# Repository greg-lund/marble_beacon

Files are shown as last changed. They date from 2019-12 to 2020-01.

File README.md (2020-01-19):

# Marble Urban Beacon Deployment System

This repository acts as an assembly guide for the COM Deployment System, and all the info that you need to build them can be found here.
For completion of this project, 20 beacons will be manufactured as well as 6-8 modified deployment systems. 
Instructions and files for the beacon are located in the beacon directory. The same is true for the deployment system. 

### BOM
The individual instruction pages include required parts, but an extensive bill of materials can be found here: <a href="https://docs.google.com/spreadsheets/d/1t7GFp-e4R7KjWGMSAGMCT9jzbI4BLS0B_l41IRGNlJQ/edit?usp=sharing" target="blank">BOM</a>.

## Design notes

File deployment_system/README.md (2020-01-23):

# Deplyoment System Assembly Instructions

All the information and part files that you need to build a deployment mechanism can be found here. I would recommend starting the 3D prints first, as the 3D prints are the most time consuming. Gathering all of the components beforehand, as well as lasercutting everything out first will make assembly much easier. 

### Parts List
Part | Quantity
-------- | --------
2020 Aluminum Extrusion | 2 x 15.75"<br>1 x 14.25"<br>3 x 10"<br>9 x 6"<br>6 x 3"
V-Slot Aluminum Extrusion | 3 x 11.75"
90&deg; 2020 bracket | 24
45&deg; 2020 bracket | 6
Nema 17 Stepper Motor | 3
Stepper Motor Bracket | 3
GT2 Pulley - 16 Tooth | 3
GT2 Idler Kit | 1
GT2 Belt x 102.5mm | 3
V-Wheel Kit | 18
M5 x 40mm Bolt | 18
M5 x 16mm Bolt | 9
M4 x 10mm Bolt | 12
M3 x 8mm Bolt | 12
M3 x 10mm Bolt | 12
M5 Spacer x 20mm | 18
M3 Spacer x 8mm | 2
M3 Spacer x 4mm | 4
CNC Shield with Arduino | 1
DRV8825 Driver Board | 3
Limit Switch Board | 3

In addition to all of the purchased components, there are various 3D printed and lasercut acrylic pieces that need to finished before the full assembly can begin. All of the files, for both 3D print and lasercut, can be found in the STL and DXF folders.

### 3D Printed Parts
Part File Name | Quantity | Notes
-------- | -------- | --------
belt\_bracket.STL | 3 | Onyx is prefered as these will be tapped<br>and support the whole weight of the beacon.
belt\_bracket\_top.STL | 3 | Onyx is prefered as these will be tapped<br>and support the whole weight of the beacon.

Assuming that assembly of the beacons have begun, you should not have to lasercut the gantry gripper piece nor the limit switch mounts. For these parts use 1/4" acrylic. All the other parts needed have been organized into a larger file to be cut out of a 12"x24" sheet. Each sheet will produce 5 of the 3 required gantry plates, and 2 of the 1 required stepper motor plate. This means that eventually 3 more of the gantry plates will need to be cut out. The individual files are also included in the directory DXF\_FULL.

### Lasercut Acrylic Pieces
Part File Name | Quantity | Notes
-------- | -------- | --------
deployment\_sheet.DXF | 1 | Use a full 1/4"x12"x24" sheet of acrylic

## Step 1: Assemble the 8020 Frame

#### Parts Needed:
- 2 x 15.75" 2020
- 1 x 14.25" 2020
- 3 x 10" 2020
- 3 x 11.75" V-Slot
- 6 x 90&deg; 2020 Bracket
- 6 x 45&deg; 2020 Bracket
- 12 x 2020 T-Slot Nut
- 12 x M5 x 8mm Bolt

Begin by tapping the ends of the 10" 2020 extrusions with an M5 tap. Assemble the frame as is shown in the drawing, below.

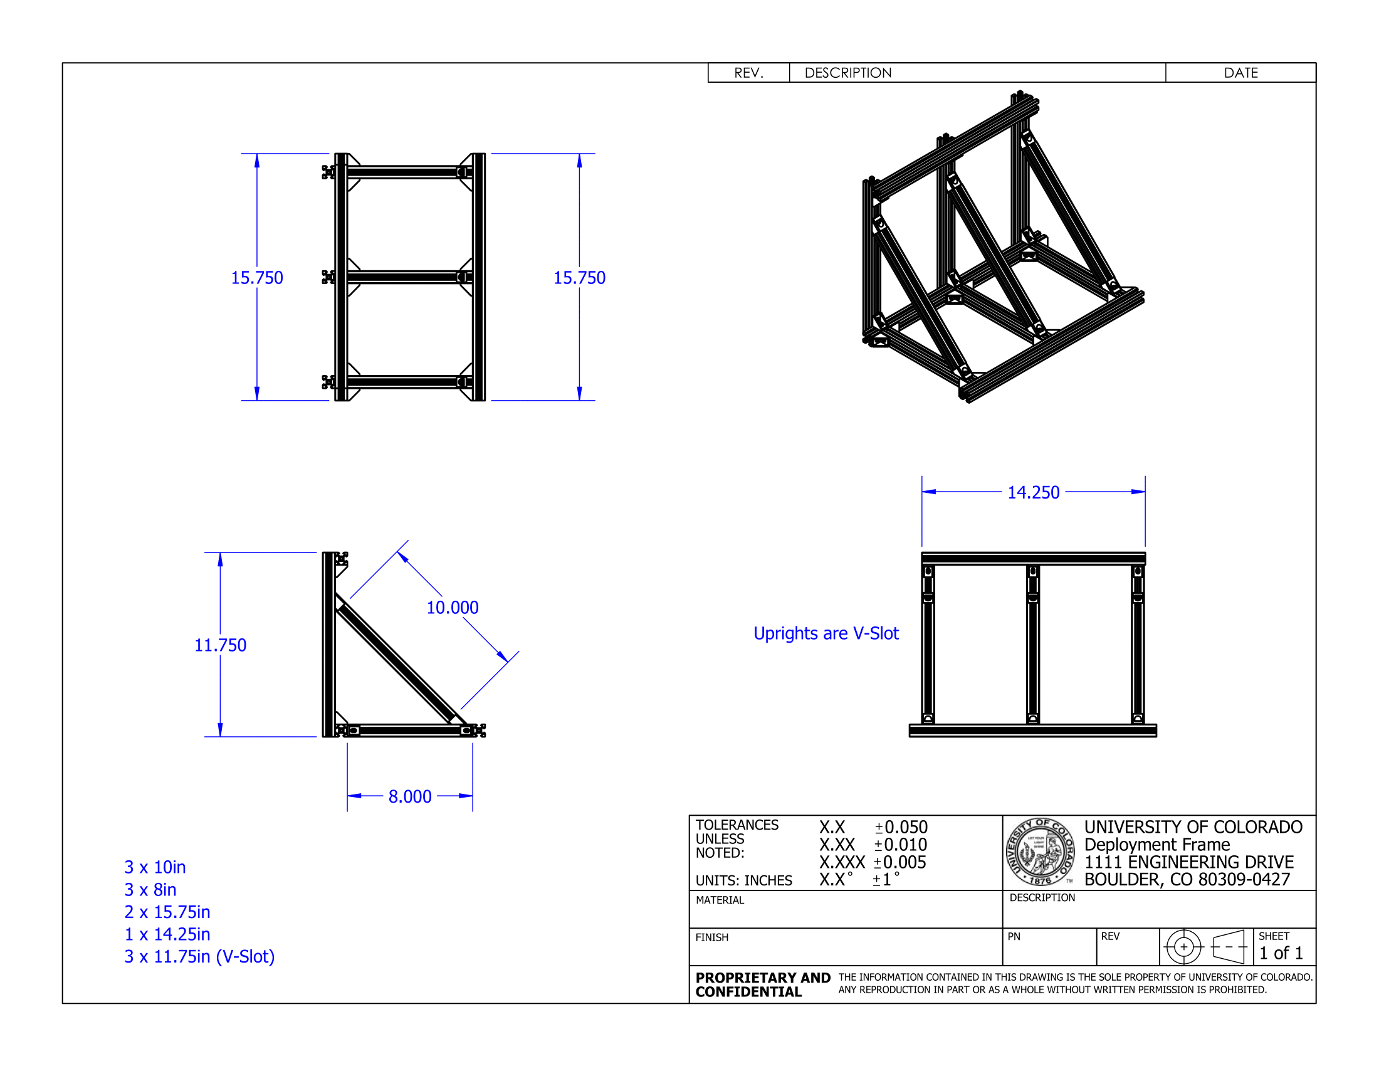
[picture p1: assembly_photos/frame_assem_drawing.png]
frame_assembly


## Step 2: Stepper Motor Mounting

#### Parts Needed:
- Stepper plate acrylic panel
- 3 x Nema 17 stepper motors
- 3 x Stepper motor bracket
- 3 x 16 tooth GT2 pulley
- 3 x T-nut and bolt
- 12 x M4 x 10mm Bolt and Nut
- 12 x M3 x 8mm Bolt and Nut
- 2020 frame assembly

Begin by attatching the motor brackets, as well as motors to the acrylic plate. Use the M4 and M3 screws here. Attach the motor assembly to the top of the frame assembly via the t-nuts and M5 holes in the plate. Attatch the pulleys at any point.

## Step 3: Fork Subassemblies

#### Parts Needed:
- 9 x 6" 2020 
- 6 x 3" 2020
- 18 x 90&deg; 2020 bracket
- 33 x T-nut and bolt
- 3 x Side plate acrylic panel
- 3 x Gantry gripper acrylic panel
- 18 x M5 x 40mm bolt
- 18 x 20mm M5 spacer
- 18 x V-Wheel kit

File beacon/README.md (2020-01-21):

# COM Beacon Assembly Instructions

All the information and part files that you need to build a COM beacon can be found here. I would recommend starting the 3D prints first, especially the electronics core rail pieces, as the 3D prints are the most time consuming. Gathering all of the components beforehand, as well as lasercutting everything out first will make assembly much easier. 

### Parts List
Part | Quantity 
-------- | --------
Power Antenna | 1
Rock64 with eMMC | 1
Battery Pack | 1
Doodle Radio | 1
12V to 5V Automotive Regulator | 1
FeatherLight Latching Relay | 1
Pushbutton with Light | 1
DPDT Switch | 2
DC Jack | 1
XT60 Connector (Male + Female) | 1
12 pin molex connector with wires (5040511201) | 1
4 Pin Molex (Male + Female) | 1
206485 9 Pin Circular Connector (Male + Female) | 1
RJ45 Connector | 1
3.5mm DC Jack - 90&deg; | 1
M2.5 Nylon Standoff and Nut | 8
M2.5 x 5mm bolt | 8
1/4" Wire Loom | 2 ft
Assorted Zipties | 

In addition to all of these purchased components, there are a variety of 3D printed and lasercut acrylic parts that need to be made before beginning the full assembly. The appropriate files for the 3D printer and lasercutter can be found in the STL and DXF directories, respectively. 

### 3D Printed Parts
Part's File Name | Quantity | Notes
-------- | -------- | --------
beacon\_foot.STL | 8 | PLA should be fine
electronics\_core\_rail.STL | 12 | PLA should be fine
lid\_bracket.STL | 1 | Use high infill or Onyx<br>as these require holes to be tapped
package\_bracket.STL | 6 | Use high infill or Onyx<br>as these require holes to be tapped

The lasercut parts for a single beacon have been organized into larger files to be cut out of 1/8"x12"x24" acrylic sheets. There are two main files that take up most of their sheets, and the electronics core must be cut separately.

### Lasercut Parts
Part's File Name | Quantity | Notes
-------- | -------- | --------
beacon\_sheet.dxf | 1 | Use a full 18"x24" sheet

The beacon\_sheet.dxf file has all of the lasercut components to create a single beacon. Take care in aligning the cut as the pieces are a tight fit on the sheet. If an individual part's DXF is required it can be found in the FULL\_DXF directory.

## Step 1: Wiring the Front Panel

#### Parts Needed:
- Pushbutton
- DC jack
- 2 x DPDT switch
- 206485 circular connector, wire mount 
- Front acrylic panel
- Assorted wire

Begin by soldering long wires onto all of the used terminals of the pushbutton, dc jack and switches. Use thicker guage for the GND, +12V and battery connections on the pushbutton and DC jack.

Mount all the components onto the front panel as shown in the photo below. Make connections and crimp connectors for the 206485 socket contacts according to the pinouts below.

#### 206485 Connector Pinout
Pin | Connection
-------- | --------
1 | +12V
2 | Battery Positive
3 | +3.3V
4 | SET
5 | GND
6 | UNSET
7 | Pi2: 3
8 | Pi2: 5
9 | NC

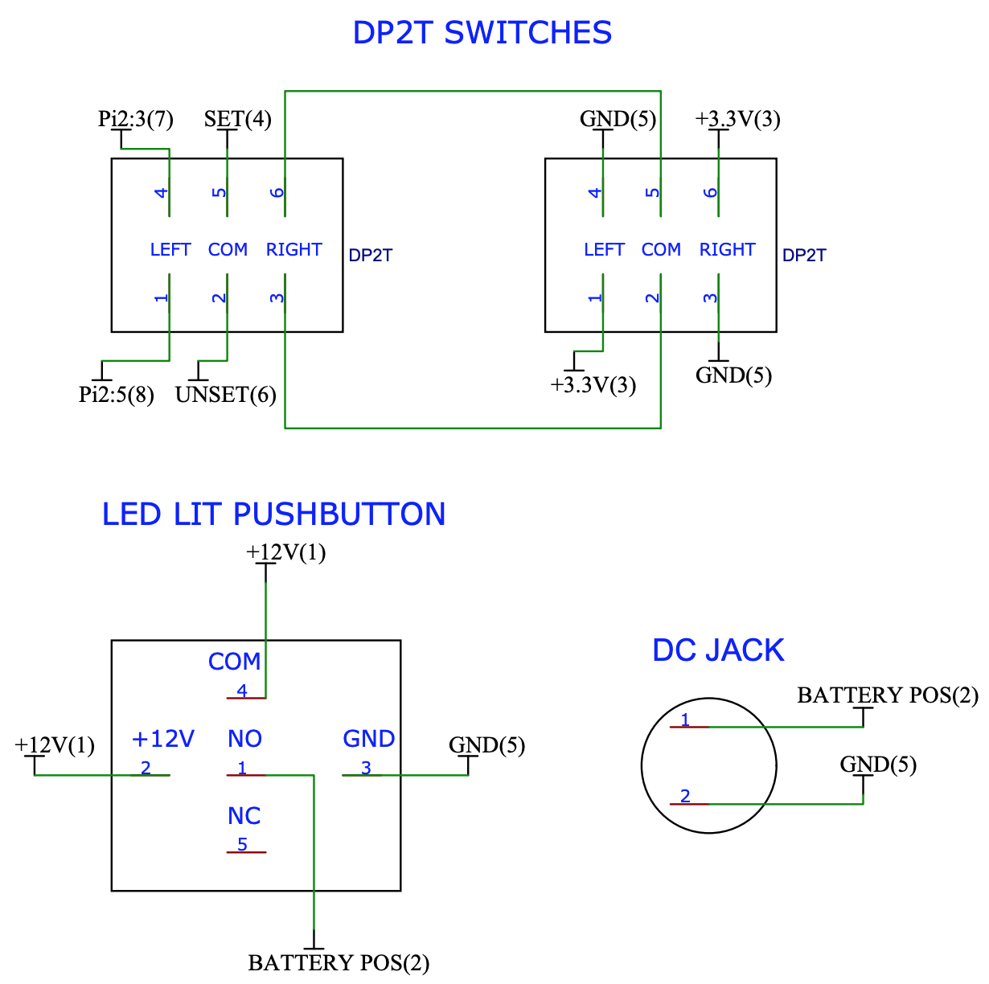
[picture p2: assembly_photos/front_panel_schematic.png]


## Step 2: Assembling the Acrylic Box

#### Parts Needed:
- The four acrylic side panels(including the wired front panel)
- Bottom acrylic panel
- 12 electronics core rail 3D prints

Begin by gluing the electronics core rail to the two identical, larger side panels. If you can't find a side plate raile template piece, lasercut one out. Line up the template with a side plate, and attach it via the two M3 screw holes. Either use superglue or acrylic cement to glue the 6 rail pieces to the plate. Don't forget to use clamps and ensure the flanges are facing eachother. Do the same on the other side, ensuring they are opposite and will fit up together.

Once the glue on the side panels has cured, glue all the pieces together, ensuring that the mounting holes for the switches and charging ports are on top and that the holes in the base plate are opposite those ports. Use either superglue or acrylic cement. Tape or clamp everything together ensuring that everything is square.

## Step 3: Assembling the Electronics Core

#### Parts Needed:
- Electronics core acrylic panel
- Battery
- XT60 pin and socket
- Rock64
- Latching relay
- Step-down converter
- Doodle radio
- 206485 panel mount connector 
- 12 pin molex connector with wires (5040511201)
- RJ45 connector
- M2.5 standoffs and screws
 
Begin by screwing all of the standoffs on to the electronics core panel. Zip tie the battery and radio, then screw down the rest of the components as shown. Solder a XT60 connector to the battery.

Wire all of the components together and crimp connections for the 206485 connector as well as the RJ45 connector. Follow the schematic below and the pinout for the 206485 connector above. Pinout diagrams for the doodle radio and RJ45 connector can be found in the wiring folder.

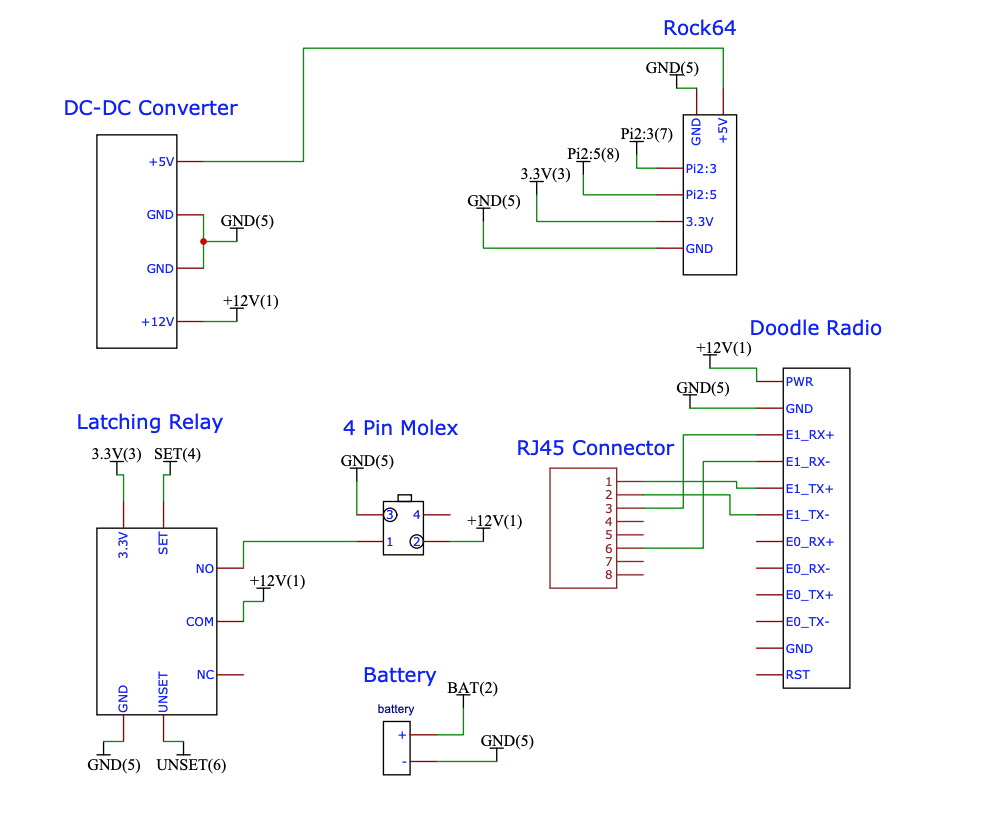
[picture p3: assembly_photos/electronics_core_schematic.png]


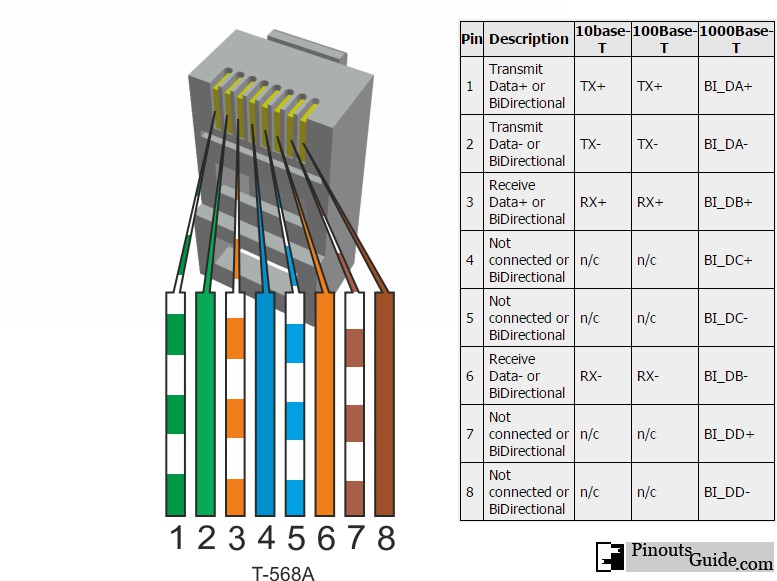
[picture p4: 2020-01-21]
beacon/wiring/rj45_pinout.jpg

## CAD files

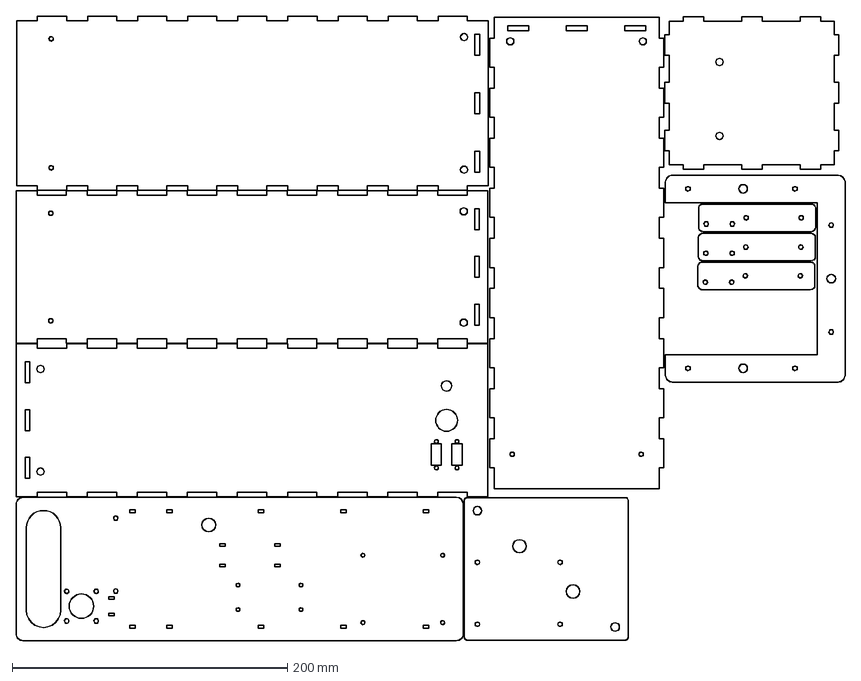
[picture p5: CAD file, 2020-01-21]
beacon/DXF/beacon_sheet.dxf
602.3 x 453.5 mm

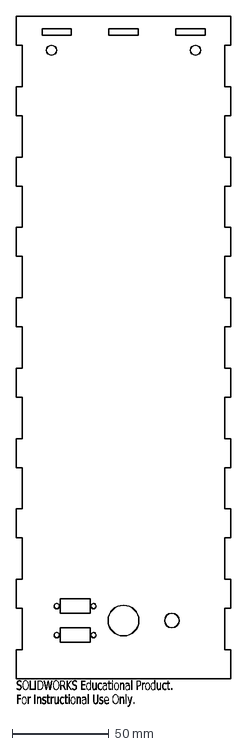
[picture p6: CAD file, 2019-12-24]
beacon/DXF/DXF_FULL/side_plate_C.DXF
SOLIDWORKS Educational Product.
For Instructional Use Only.

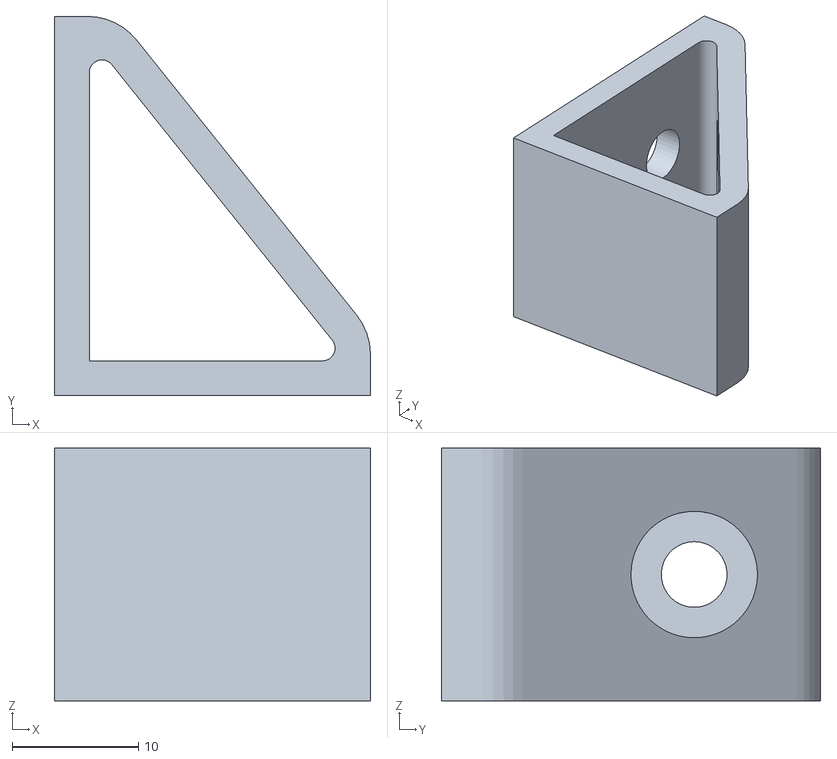
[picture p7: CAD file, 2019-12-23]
beacon/STL/beacon_foot.STL
25.0 x 30.0 x 20.0

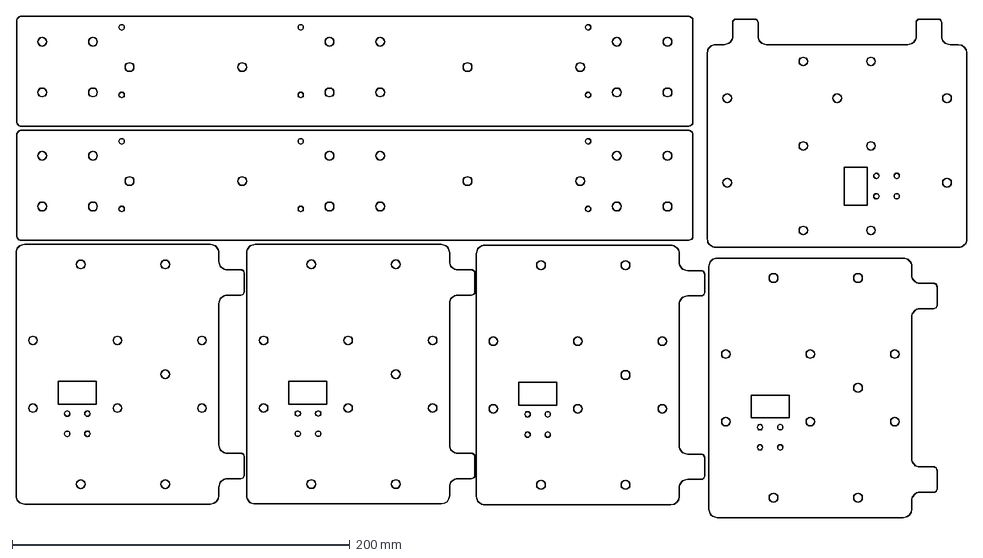
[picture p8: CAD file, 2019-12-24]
deployment_system/DXF/deployment_sheet.dxf
562.6 x 296.6 mm

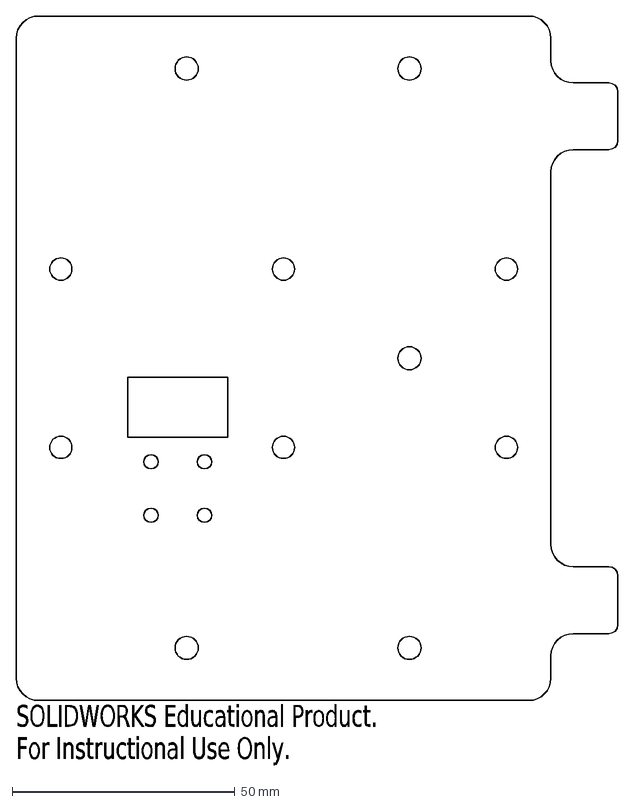
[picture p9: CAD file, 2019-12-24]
deployment_system/DXF/DXF_FULL/side_plate.DXF
SOLIDWORKS Educational Product.
For Instructional Use Only.

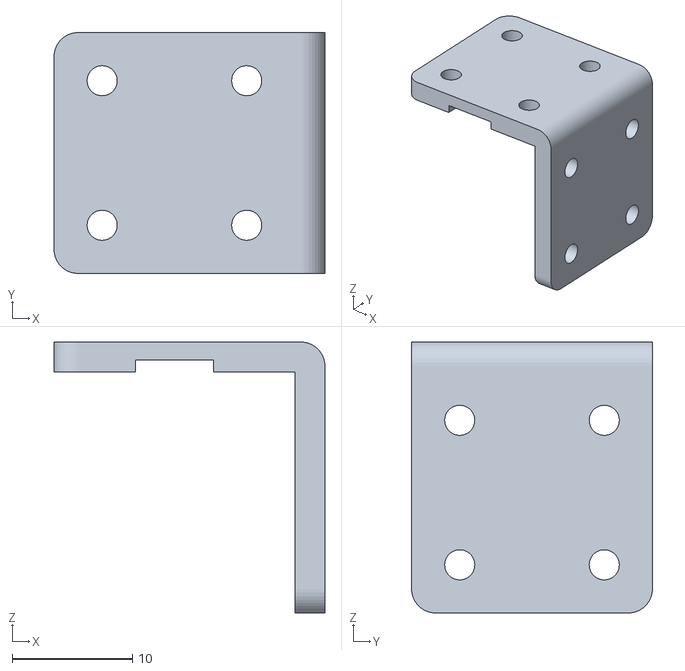
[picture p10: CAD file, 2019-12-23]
deployment_system/STL/belt_bracket.STL
22.5 x 20.0 x 22.5

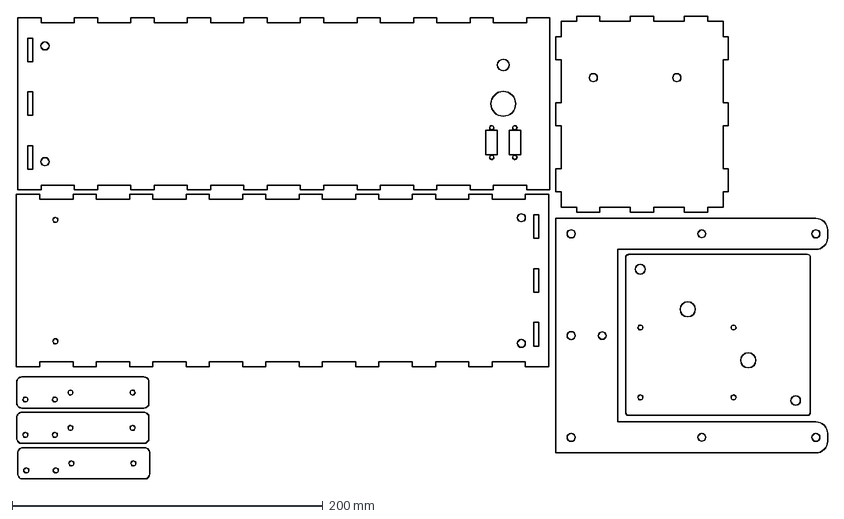
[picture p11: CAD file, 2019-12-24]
beacon/DXF/beacon_sheet_1.dxf
522.0 x 297.9 mm

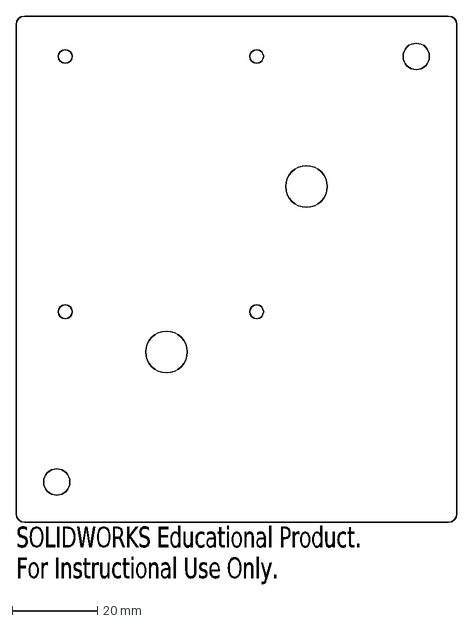
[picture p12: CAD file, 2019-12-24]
beacon/DXF/DXF_FULL/top_plate.DXF
SOLIDWORKS Educational Product.
For Instructional Use Only.

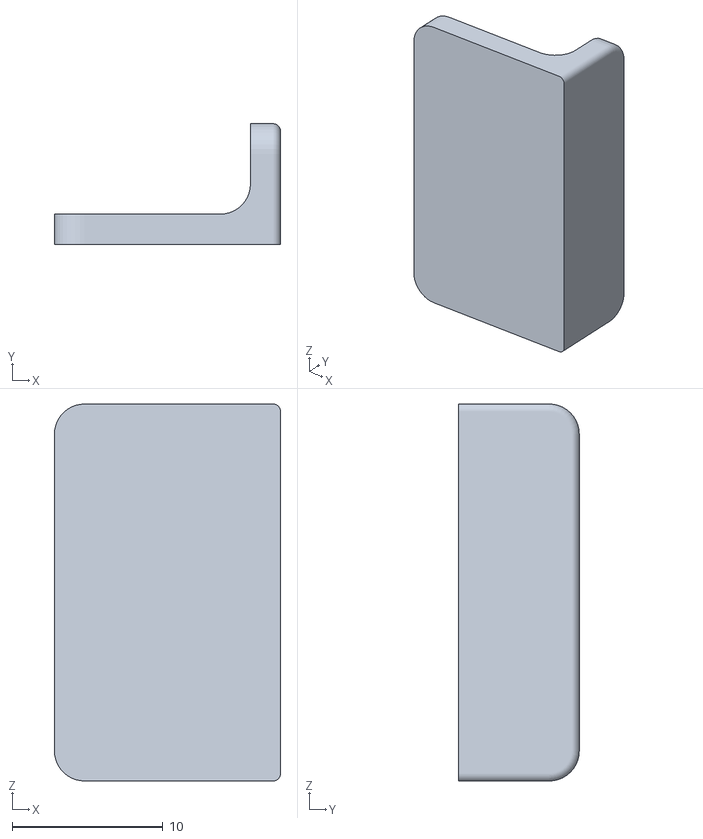
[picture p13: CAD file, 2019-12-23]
beacon/STL/electronics_core_rail.STL
15.0 x 8.00 x 25.0

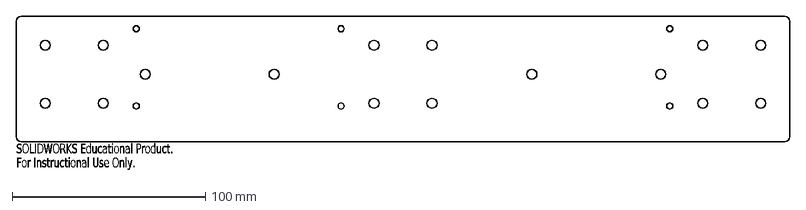
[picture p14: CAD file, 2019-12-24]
deployment_system/DXF/DXF_FULL/stepper_plate.DXF
SOLIDWORKS Educational Product.
For Instructional Use Only.

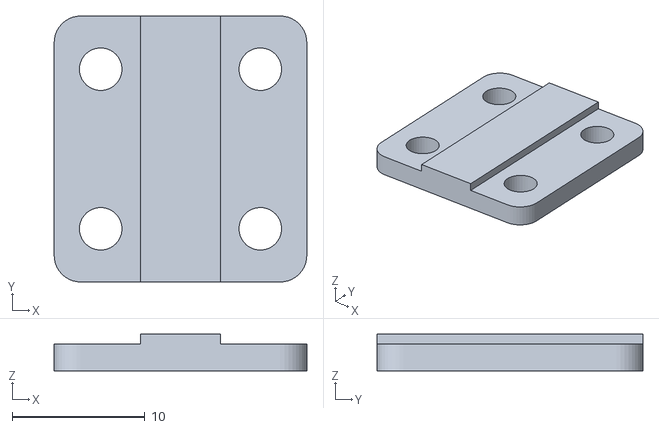
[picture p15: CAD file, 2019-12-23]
deployment_system/STL/belt_bracket_top.STL
19.0 x 20.0 x 2.75

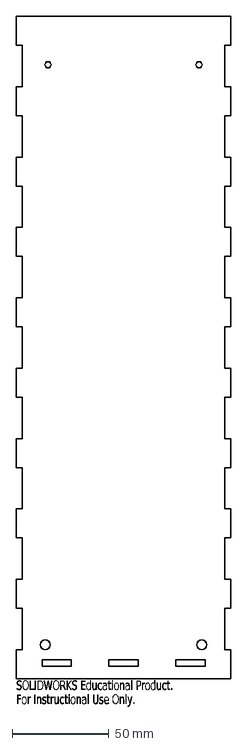
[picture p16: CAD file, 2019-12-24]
beacon/DXF/DXF_FULL/side_plate_B.DXF
SOLIDWORKS Educational Product.
For Instructional Use Only.

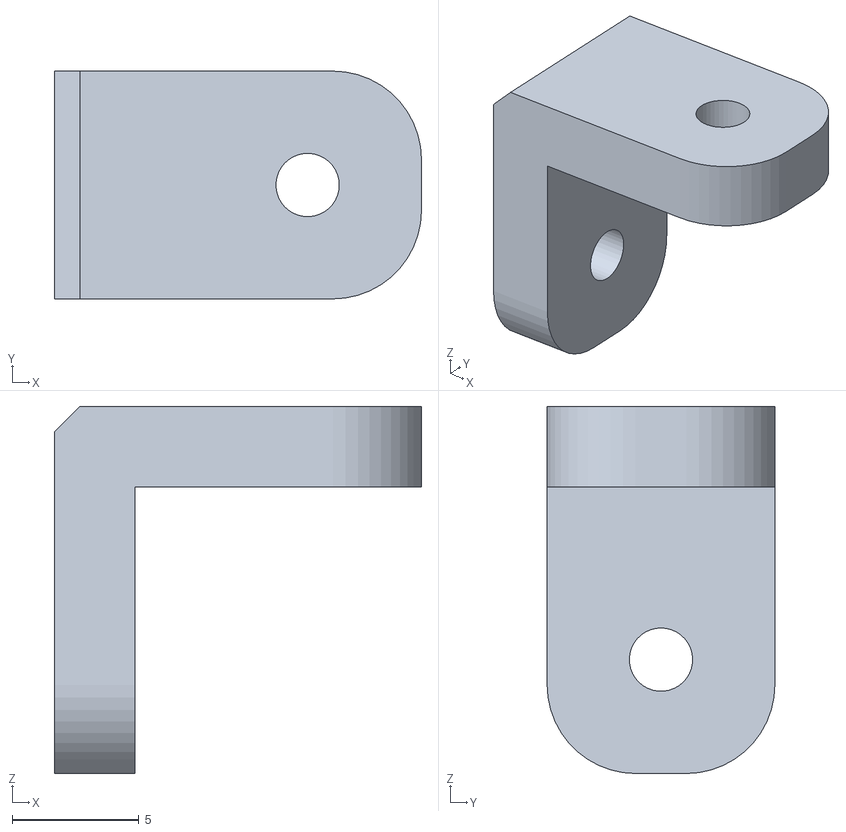
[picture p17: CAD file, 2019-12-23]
beacon/STL/package_bracket.STL
14.5 x 9.00 x 14.5

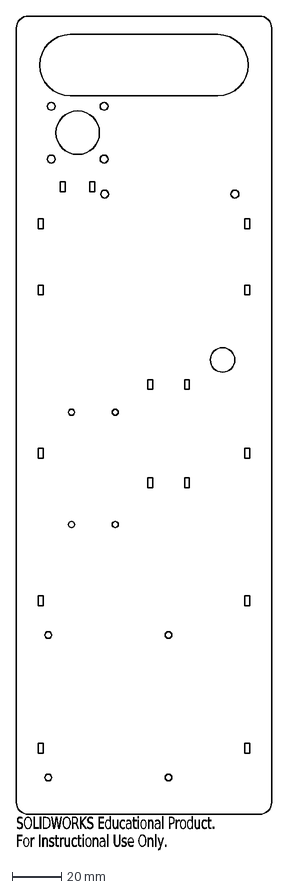
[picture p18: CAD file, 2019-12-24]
beacon/DXF/DXF_FULL/electronics_core.DXF
SOLIDWORKS Educational Product.
For Instructional Use Only.

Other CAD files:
beacon/STL/lid_bracket.STL
beacon/DXF/DXF_FULL/side_plate_A.DXF
beacon/DXF/DXF_FULL/base_plate.DXF
beacon/DXF/DXF_FULL/side_plate_rail_template.DXF
beacon/DXF/DXF_FULL/package_fork.DXF

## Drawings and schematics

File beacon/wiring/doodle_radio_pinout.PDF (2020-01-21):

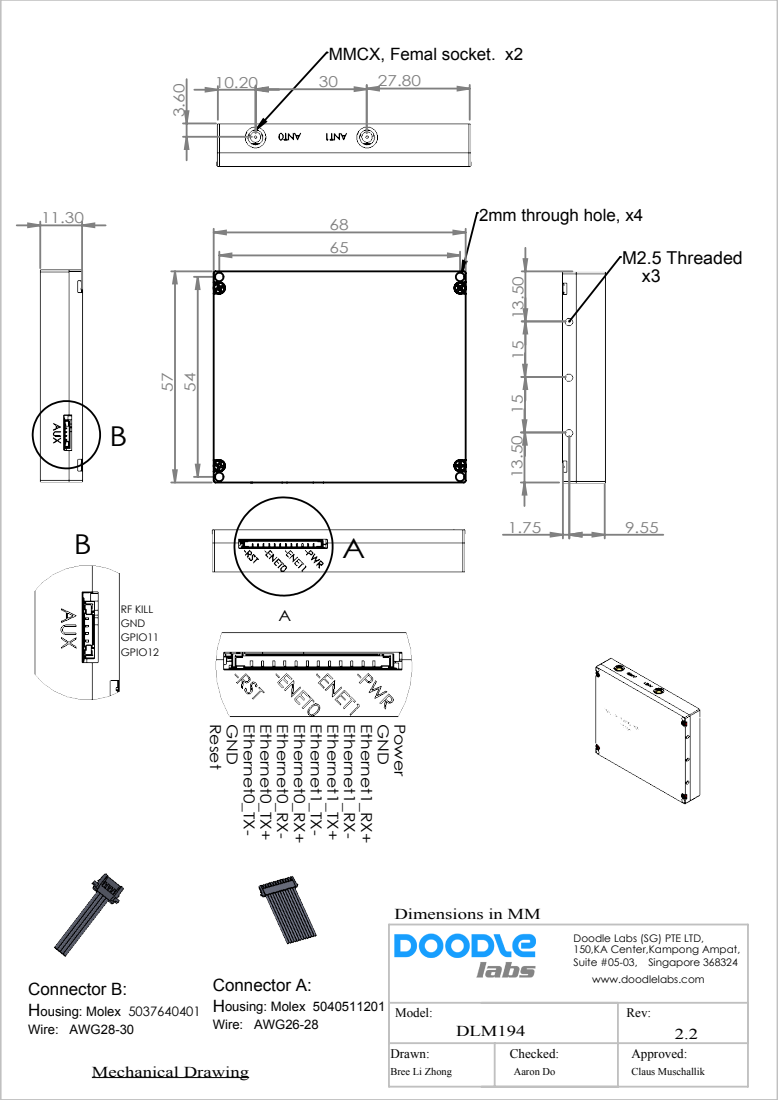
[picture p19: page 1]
M2.5 Threaded; 2mm through hole, x4; Connector A: Housing: Molex 5040511201 Wire: AWG26-28; RF KILL; Connector B: Housing: Molex 5037640401 Wire: AWG28-30; Singapore 368324; Mechanical Drawing

MMCX, Femal socket. x2

Dimensions in MM

Doodle Labs (SG) PTE LTD,
150,KA Center,Kampong Ampat,
Suite #05-03,
www.doodlelabs.com

Model: DLM194 | Rev: 2.2

Drawn: Bree Li Zhong | Checked: Aaron Do | Approved: Claus Muschallik

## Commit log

2019-12-24 Added DXF
    [base_plate.DXF, beacon_sheet_1.dxf, beacon_sheet_2.dxf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]
2019-12-24 Deployment Instructions
    [deployment_sheet.dxf, side_plate.DXF, stepper_plate.DXF]
2020-01-21 Updated beacon dxf sheet
    [beacon_sheet.dxf, beacon_sheet_2.dxf, electronics_core.DXF]
2020-01-21 Updated beacon dxf
    [beacon_sheet.dxf]
2020-01-21 Added schematic
2020-01-21 updated schematic
2020-01-23 Added belt length
